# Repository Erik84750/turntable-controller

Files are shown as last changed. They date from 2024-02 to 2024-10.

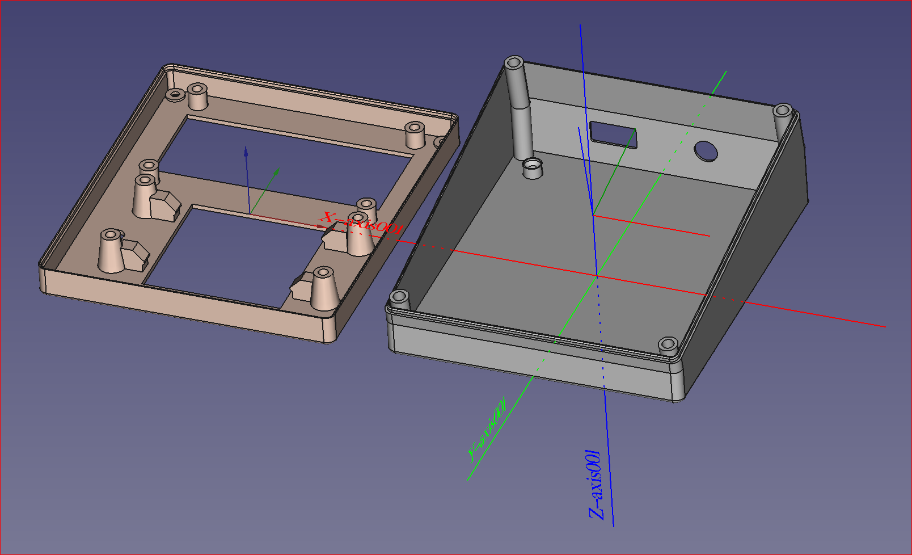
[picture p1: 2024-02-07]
turntable_controller_complete.png

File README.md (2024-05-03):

# turntable-controller
Digital stand-alone turntable controller with automated indexing and stepper motor

A. Introduction
  1. The purpose of this project is to create a stand-alone and automated model railroad (any scale) turntable controller
  2. Hardware: 

  a. stepper motor: project is usable for any type of stepper motor but prefered option is the use of a 17HS2408 motor (NEMA17).

  b. stepper motor driver: any motor driver module can be used but prefered option is a module with an onboard A4988 chip (https://lastminuteengineers.com/a4988-stepper-motor-driver-arduino-tutorial/).
    
  c. indexing sensor: optical HC-020K sensor with accurate positioning sensing; only the sensor (no perforated disks). Hall effect is exluded due to its inacurate sensing repeatability and wide detection range.
  The turntable disk should be equipped with just one small protruding object that passes through the sensor "eye", mounted underneath the framework, out of sight.
  The purpose being that this object passes through the sensor eye once every 360 degree rotation of the turntable.
This object may even be the size of a nail; as long as it passes through the sensor lips.
    
  d. 4x4 keypad with pushbuttons (no membrane keypad).
    
  e. a custom designed PCB (all required info for manufacture is included in this project file).
    
  f. LCD display with 20x4 characters.
    
  g. a 3D printable casing for this project, downloadable .stl files.

  h. turntable track polarity control: ACS712-based sensor controls the DCC track polarity. Omron G6S-2 5VDC relay. Measured reaction time is 2 microseonds (using AVR AtMega328 at 16MHs)! Therefor it beats every short-circuit or overload detection including the DCC-EX Command Station.
    
  3. Software
    a. C++ custom software with a very wide range of options and features
    b. All software is freely downloadable from this project file

B. Description of features:
  1. Any size of turntable can be controlled
  2. Automated initial indexing and storage in eeprom is provided. Due to the very high accuracy (+/- 1 micrometer) of the optical sensor the repeatability is < 5 micrometer.
  3. Fast index location and programming for outgoing/incoming tracks is provided, storage in eeprom. The turntable will always move CW or CCW after the algorithm included calculates the shortest/fastest rotation
  4. Automated "shortest rotation" algorithm is included in the software
  5. Photo-electric sensor (based on HC-020K module) http://tinyurl.com/2ce3v4j9 or http://tinyurl.com/3nykkvw3 used for indexing calibration
  6. button A: assign the current position to an index number in eeprom
  7. button B: move to whatever position by using the keypad
  8. button C: calibration
  9. button D: designate a position (current position) from eeprom to current turntable indexed position
  11. button #: select an index position to be moved to
  12. Button *: select index position + 180° to be moved to.
  13. enter # or * before index selection so that the turntable alligns at 0° or 180°
  14. Rotary encoder rotation of turntable; RE button serves to set speed x10 or regular
  15. a "long press" of (adjustable) 500ms is included to prevent inadvertent keypresses
  16. include, upon calibration, the option to make a full 360° in order to calculate the stepper motor steps for a full 360° rotation.
  17. EEPROM storage of programmed track index positions

C. Documents

[stepper motor 17HS2408-MotionKing.pdf](https://github.com/Erik84750/turntable-controller/files/14192960/stepper.motor.17HS2408-MotionKing.pdf)

[stepper motor driver A4988.pdf](https://github.com/Erik84750/turntable-controller/files/14192971/stepper.motor.driver.A4988.pdf)

[Uploading stepper motor 28BYJ-45 12V.pdf…]()

stepper motor HS2236_1

a4988-stepper-motor-controler

md-hc-020k

keypad 4x4

turntable_controller_complete



ACS712

Omron_G6S-2_5VDC

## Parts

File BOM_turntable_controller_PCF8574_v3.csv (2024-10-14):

Part | Value | Device | Package | Description | AVAILABILITY | DESCRIPTION | MF | MP | MPN | OC_FARNELL | OC_NEWARK | PACKAGE | PRICE | PURCHASE-URL
C1 | 47µF | CERAMIC-CAP | 1206 | ceramic capacitor leads 2.5mm and 5.5mm
C2 | 1µF | CERAMIC-CAP | 1206 | ceramic capacitor leads 2.5mm and 5.5mm
C3 | 100µF | CERAMIC-CAP | 1206 | ceramic capacitor leads 2.5mm and 5.5mm
C12 | 100µF | ELCOELCO3,5MMLEAD | ELCO-3.5MMLEAD | electrolytic capacitor 3.5mm lead
D1 | SCHOTTKY-SMA | SCHOTTKY-SMA | SMA-ALT | Schottky diode SMA package
D2 | pwr | LED-0603V1 | LED_0603 | LED SMD mount
D3 | SCHOTTKY-SMA | SCHOTTKY-SMA | SMA-ALT | Schottky diode SMA package
D4 |  | LED-0603V1 | LED_0603 | LED SMD mount
D5 |  | LED-0603V1 | LED_0603 | LED SMD mount
D6 |  | LED-0603V1 | LED_0603 | LED SMD mount
D7 |  | LED-0603V1 | LED_0603 | LED SMD mount
D8 | STEP | LED-0603V1 | LED_0603 | LED SMD mount
D9 | DIR | LED-0603V1 | LED_0603 | LED SMD mount
D10 | Enbl. | LED-0603V1 | LED_0603 | LED SMD mount
D11 | Vmot | LED-0603V1 | LED_0603 | LED SMD mount
IC1 | ARDUINO-PRO-MINI-LIMITED | ARDUINO-PRO-MINI-LIMITED | ARDUINO-PRO-MINI-LIMITED | Arduino Pro Mini Clone V1.0
IC2 | 7805 | LM78XX-TO220SINK_V2 | LM7805-SINK_V2 | LM1117 TO220 VOLTAGE REGULATOR
IC3 | PCF8574T | PCF8574T | SOIC127P1032X265-16N | Remote 8-bit I/O expander for I2C-bus Check availability | Not in stock | I/O Expander 8 I²C 100 kHz 20-SSOP | NXP Semiconductors | PCF8574T |  |  |  | SOIC-16 NXP Semiconductors | None
IC4 | ULN2003 | ULN2003 | SO16
JP1 | MS1 | JUMPER-SMT_2_NO_SILK | SMT-JUMPER_2_NO_SILK | Normally open jumper
JP2 | MS2 | JUMPER-SMT_2_NO_SILK | SMT-JUMPER_2_NO_SILK | Normally open jumper
JP3 |  | PINHD-1X2 | 1X02 | PIN HEADER
JP4 |  | PINHD-1X2 | 1X02 | PIN HEADER
JP5 |  | PINHD-1X8 | 1X08 | PIN HEADER
JP6 | MS3 | JUMPER-SMT_2_NO_SILK | SMT-JUMPER_2_NO_SILK | Normally open jumper
JP7 |  | PINHD-1X2 | 1X02 | PIN HEADER
JP9 |  | JUMPER-SMT_2_NO_SILK | SMT-JUMPER_2_NO_SILK | Normally open jumper
JP10 |  | JUMPER-SMT_2_NO_SILK | SMT-JUMPER_2_NO_SILK | Normally open jumper
JP11 |  | JUMPER-SMT_2_NO_SILK | SMT-JUMPER_2_NO_SILK | Normally open jumper
JP12 |  | JUMPER-SMT_2_NO_SILK | SMT-JUMPER_2_NO_SILK | Normally open jumper
R1 | 10k | RESISTORARRAY-0603 | RESISTORARRAY-0603 | Res Thick Film Array 100 Ohm 5% ?200ppm/C ISOL Epoxy 8-Pin 1206(4 X 0603) Convex SMD T/R Check availability | In Stock | 330 Ohm ±5% 62.5mW Power Per Element Isolated 4 Resistor Network/Array ±200ppm/°C 1206 (3216 Metric), Convex, Long Side Terminals | Yageo | YC164-JR-07330RL |  |  |  | 1206 Yageo | None | https://pricing.snapeda.com/search/part/YC164-JR-07330RL/?ref=eda
R2 | 4k7 | RESISTORARRAY-0603 | RESISTORARRAY-0603 | Res Thick Film Array 100 Ohm 5% ?200ppm/C ISOL Epoxy 8-Pin 1206(4 X 0603) Convex SMD T/R Check availability | In Stock | 330 Ohm ±5% 62.5mW Power Per Element Isolated 4 Resistor Network/Array ±200ppm/°C 1206 (3216 Metric), Convex, Long Side Terminals | Yageo | YC164-JR-07330RL |  |  |  | 1206 Yageo | None | https://pricing.snapeda.com/search/part/YC164-JR-07330RL/?ref=eda
R3 | 10k | RESISTOR-SMD-1206 | R1206W | Resistor 1/4W H wide fit
R5 | 10k | RESISTOR-SMD-1206 | R1206W | Resistor 1/4W H wide fit
R6 | 4k7 | RESISTORARRAY-0603 | RESISTORARRAY-0603 | Res Thick Film Array 100 Ohm 5% ?200ppm/C ISOL Epoxy 8-Pin 1206(4 X 0603) Convex SMD T/R Check availability | In Stock | 330 Ohm ±5% 62.5mW Power Per Element Isolated 4 Resistor Network/Array ±200ppm/°C 1206 (3216 Metric), Convex, Long Side Terminals | Yageo | YC164-JR-07330RL |  |  |  | 1206 Yageo | None | https://pricing.snapeda.com/search/part/YC164-JR-07330RL/?ref=eda
U$9 | JST-XH-5 | JST-XH-5 | B5B-XH-A
U1 | A4988 | A4988 | A4988 | Stepper motor controler; IC: A4988; 1A; Uin mot: 8÷35V Check availability | Not in stock | Stepper Motor Driver | Pololu | A4988 STEPPER MOTOR DRIVER CARRIER |  |  |  | None | None
X1 |  | TERMINAL-5MM-2POLE | W237-132 | WAGO SREW CLAMP |  |  |  |  |  | unknown | unknown
X2 | TERMINAL_2P_3,5MM_V2 | TERMINAL_2P_3,5MM_V2 | TERMINAL_2P_3,5MM_V2 | MKDS 1/ 2-3,5 Printklemme |  |  |  |  |  | unknown | unknown
X3 | TERMINAL_2P_3,5MM_V2 | TERMINAL_2P_3,5MM_V2 | TERMINAL_2P_3,5MM_V2 | MKDS 1/ 2-3,5 Printklemme |  |  |  |  |  | unknown | unknown
X4 | TERMINAL_2P_3,5MM_V2 | TERMINAL_2P_3,5MM_V2 | TERMINAL_2P_3,5MM_V2 | MKDS 1/ 2-3,5 Printklemme |  |  |  |  |  | unknown | unknown
X5 | TERMINAL_2P_3,5MM_V2 | TERMINAL_2P_3,5MM_V2 | TERMINAL_2P_3,5MM_V2 | MKDS 1/ 2-3,5 Printklemme |  |  |  |  |  | unknown | unknown
X6 | TERMINAL_2P_3,5MM_V2 | TERMINAL_2P_3,5MM_V2 | TERMINAL_2P_3,5MM_V2 | MKDS 1/ 2-3,5 Printklemme |  |  |  |  |  | unknown | unknown
X7 | TERMINAL_2P_3,5MM_V2 | TERMINAL_2P_3,5MM_V2 | TERMINAL_2P_3,5MM_V2 | MKDS 1/ 2-3,5 Printklemme |  |  |  |  |  | unknown | unknown
X8 |  | TERMINAL-5MM-2POLE | W237-132 | WAGO SREW CLAMP |  |  |  |  |  | unknown | unknown
X9 | TERMINAL_2P_3,5MM_V2 | TERMINAL_2P_3,5MM_V2 | TERMINAL_2P_3,5MM_V2 | MKDS 1/ 2-3,5 Printklemme |  |  |  |  |  | unknown | unknown
X10 | TERMINAL_2P_3,5MM_V2 | TERMINAL_2P_3,5MM_V2 | TERMINAL_2P_3,5MM_V2 | MKDS 1/ 2-3,5 Printklemme |  |  |  |  |  | unknown | unknown
X11 | TERMINAL_2P_3,5MM_V2 | TERMINAL_2P_3,5MM_V2 | TERMINAL_2P_3,5MM_V2 | MKDS 1/ 2-3,5 Printklemme |  |  |  |  |  | unknown | unknown
X12 | TERMINAL_2P_3,5MM_V2 | TERMINAL_2P_3,5MM_V2 | TERMINAL_2P_3,5MM_V2 | MKDS 1/ 2-3,5 Printklemme |  |  |  |  |  | unknown | unknown
X13 | TERMINAL_2P_3,5MM_V2 | TERMINAL_2P_3,5MM_V2 | TERMINAL_2P_3,5MM_V2 | MKDS 1/ 2-3,5 Printklemme |  |  |  |  |  | unknown | unknown
X14 | JST-XH-04 | JST-XH-04 | B4B-XH-A | JST XH Connector 2 Pin

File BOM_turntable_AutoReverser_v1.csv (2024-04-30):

Part | Value | Device | Package | Description | MF | MPN | OC_FARNELL | OC_NEWARK
C1 | 100µF | CERAMIC-CAP | 1206 | ceramic capacitor leads 2.5mm and 5.5mm
D2 | LED-0603 | LED-0603V1 | LED_0603 | LED SMD mount
D3 | 1N4148 | 1N4148SOD323-ST | SOD323_ST | DIODE
IC1 | ARDUINO-PRO-MINI-LIMITED | ARDUINO-PRO-MINI-LIMITED | ARDUINO-PRO-MINI-LIMITED | Arduino Pro Mini Clone V1.0
IC2 | LM7111-5V | LM1117-TO220 | TO220V | LM1117 TO220 VOLTAGE REGULATOR
JP1 |  | PINHD-1X3 | 1X03 | PIN HEADER
K1 | OMRON_RELAY_TX25VD2 | OMRON_RELAY_TX25VD2 | RELAY | TX Relais NAiS |  | TXD2-5V | unknown
Q1 | AO3400A | AO3400A-N-CH | SOT23 | AO3400 N-channel 30V TTL MOSFET
R1 | 1k | RESISTOR-SMD-1206 | R1206W | Resistor 1/4W H wide fit
R2 | 1k | RESISTOR-SMD-1206 | R1206W | Resistor 1/4W H wide fit
SJ1 |  | SJ | SJ | SMD solder JUMPER
X1 | TERMINAL_2P_3,5MM_V2 | TERMINAL_2P_3,5MM_V2 | TERMINAL_2P_3,5MM_V2 | MKDS 1/ 2-3,5 Printklemme |  |  | unknown | unknown
X2 | TERMINAL_2P_3,5MM_V2 | TERMINAL_2P_3,5MM_V2 | TERMINAL_2P_3,5MM_V2 | MKDS 1/ 2-3,5 Printklemme |  |  | unknown | unknown
X5 |  | TERMINAL-5MM-2POLE | W237-132 | WAGO SCREW CLAMP |  |  | unknown | unknown
X6 |  | TERMINAL-5MM-2POLE | W237-132 | WAGO SCREW CLAMP |  |  | unknown | unknown

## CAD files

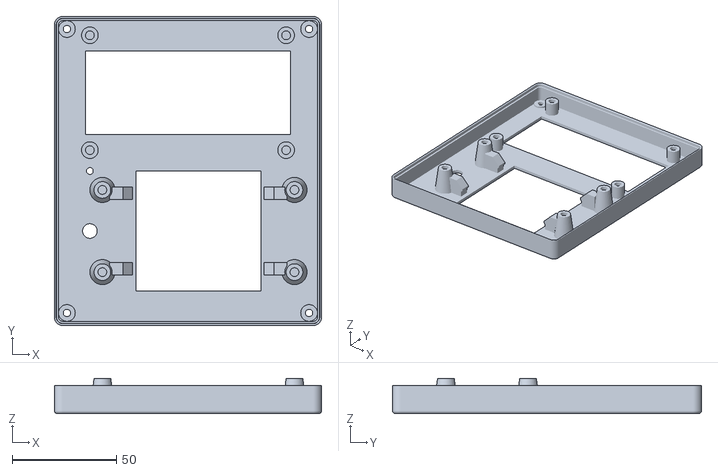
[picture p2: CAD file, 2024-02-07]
turntable_controller_v2-cover.stl
128.0 x 148.0 x 17.0

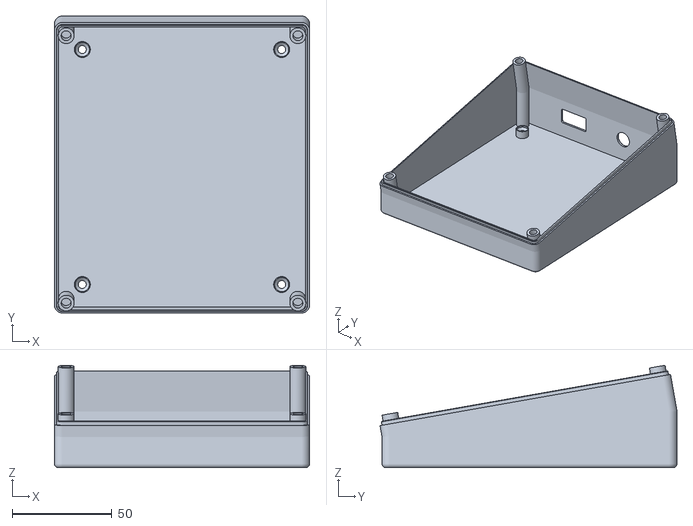
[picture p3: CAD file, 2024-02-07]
turntable_controller_v2-bottom.stl
128.0 x 149.0 x 51.4

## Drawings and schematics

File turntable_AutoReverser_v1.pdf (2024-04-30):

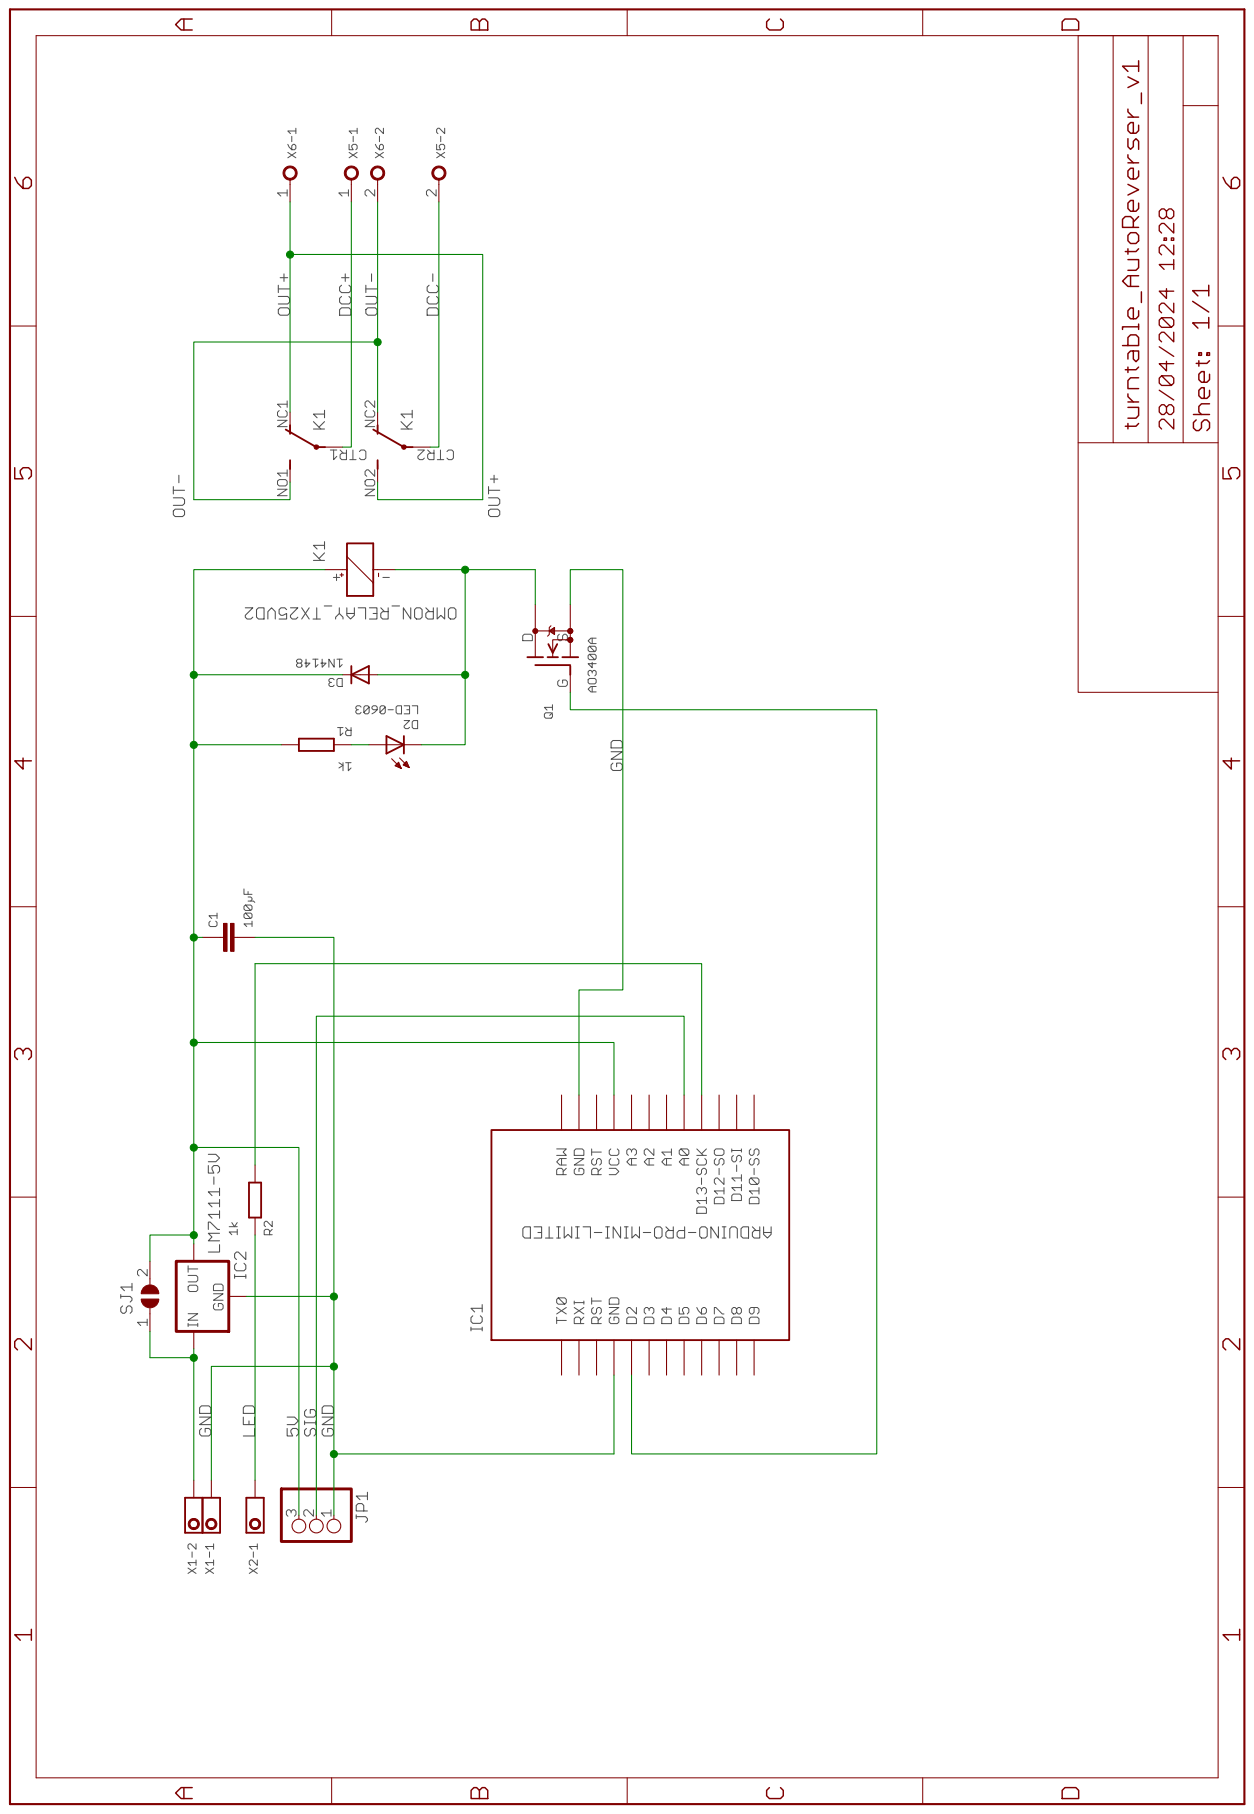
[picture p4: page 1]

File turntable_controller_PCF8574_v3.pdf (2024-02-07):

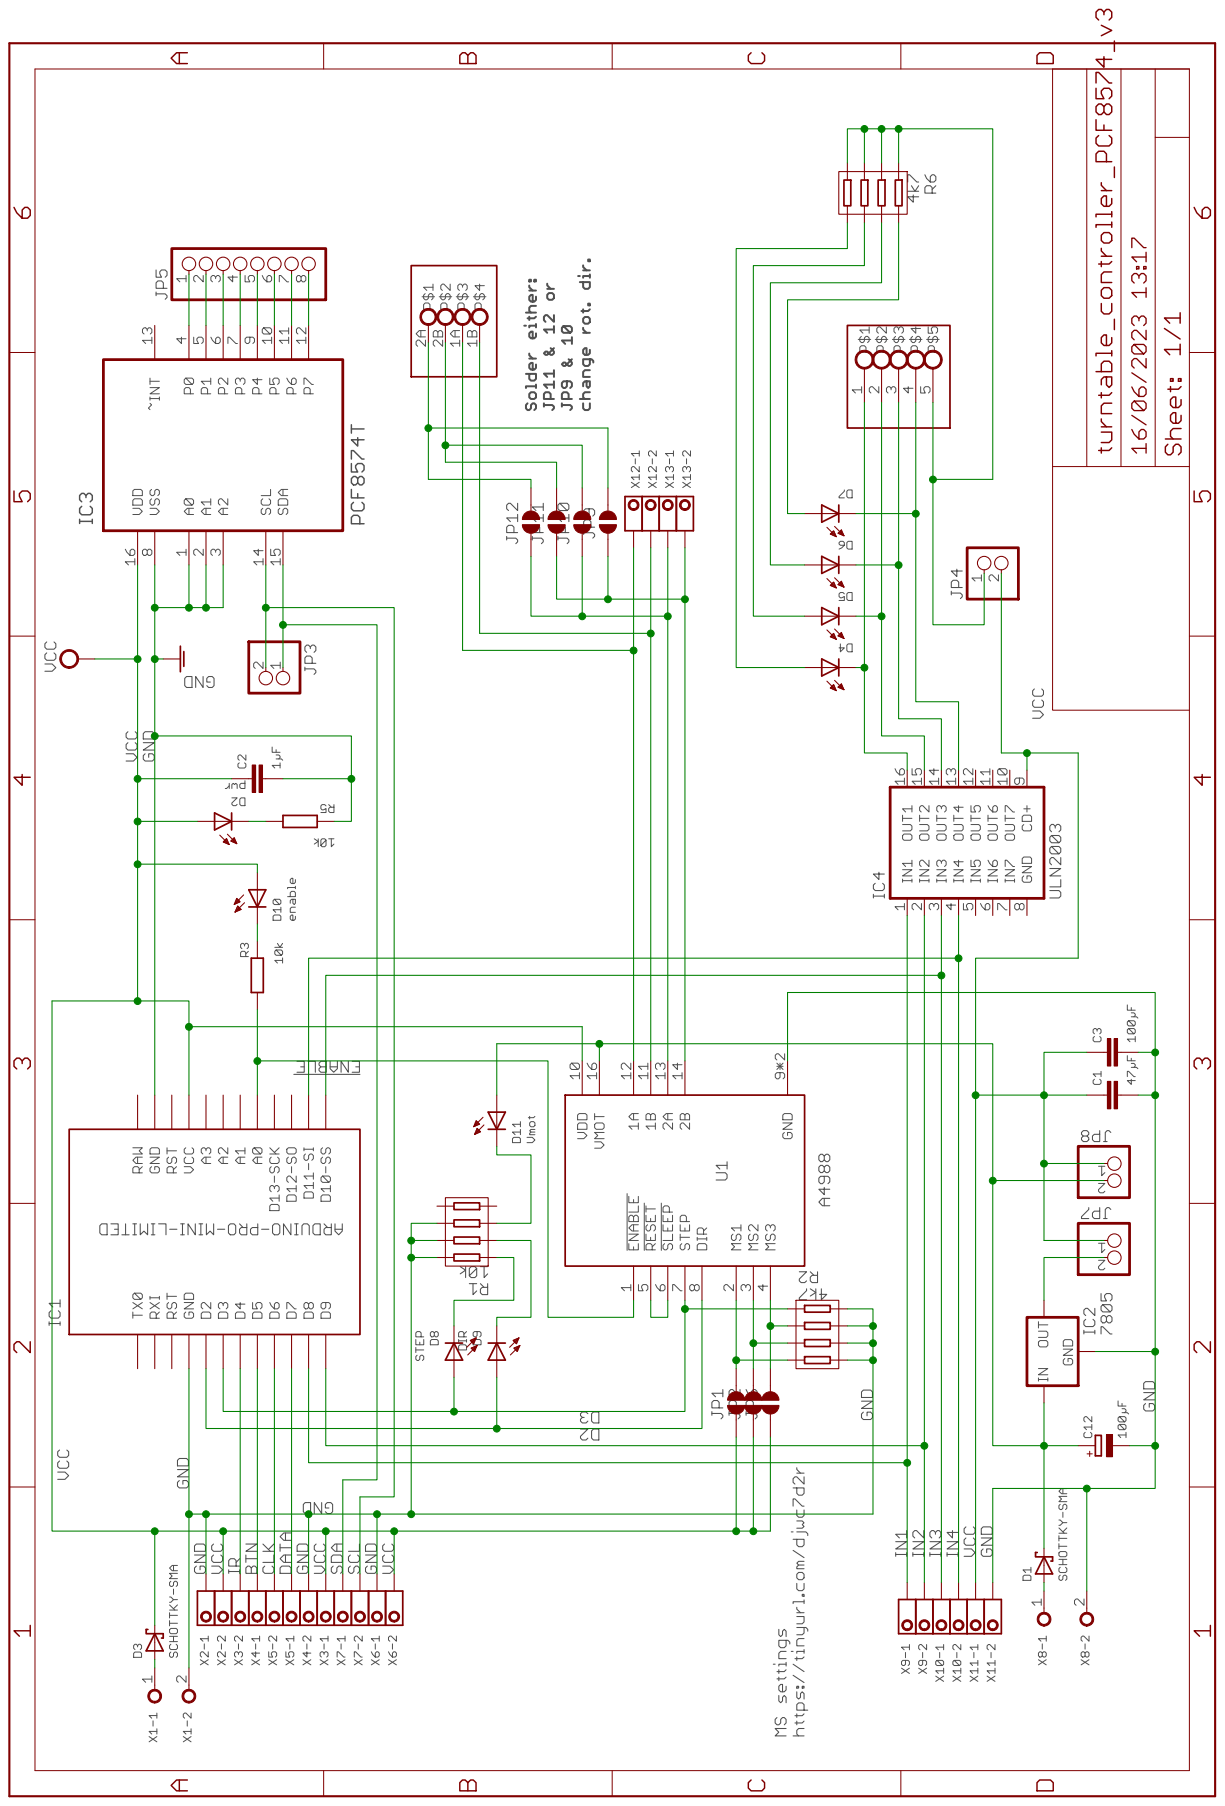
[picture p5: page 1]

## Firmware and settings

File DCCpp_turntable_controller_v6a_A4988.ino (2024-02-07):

/*
  Read keypad: if number pressed then two keypad strokes required; else just one stroke
  Store keypad numerical entry for
     OBSOLETE 1. either turntable index position (moveTo
     OBSOLETE 2. or store in EEPROM after 'A' is pressed
  Store character entry for:
     A = Assign current position (currentPosition) into eeprom for an index number (index to be entered)
     B = move to whatever position value is entered in keypad
          # = validate numerical entry (for >2 digits only; ie: case B
            = erase last numerical entry, for case B only
     C = calibration of '0' index position; optionally turn table 360 degrees to calculate number of steps needed for 180 degrees
     D = Designate a position (setCurrentPosition) from eeprom to current turntable indexed position (index to be entered):
         done at program startup when stepper is in a known and indexed position
     # = select index position to be moved to
     * = select index position + 180 degrees to be moved to

       NOTE: v5 : precede index with either # or * to decide allignement of turntable at 0 or 180 degrees

  Version v5:
  1. also allow indexposition + 180 degrees: allow the turntable to make a half turn on the same index
  2. index selection: now precede with either # or  * to decide whether turntable alligns at 0 degrees ort 180 degrees

  Version v6:
     1. done: to do: on calibration give option to make a full 360 degree turn, to count the number of required steps.
     This in order to calculate the number of steps needed to make a 18 degree swing
     2. to do: index selection: now precede with either # or  * to decide whether turntable alligns at 0 degrees or 180 degrees
     3. done: to do: optimize index search (see 2.) for minimum distance movement (algorithm)
     4. done: introduce a "long press" for keypad characters: https://arduinogetstarted.com/tutorials/arduino-button-long-press-short-press
     5. introduce a turntable movement interruption, for example when wrong index is selected; to avoid having to wait for turntable to finalise the wrong move

  Version 6a:
     1. modified algorithm "shortest move" to accomodate for the special case (re Thomas 9/6/23)

  Turntable notes: 120' scale Diamond Scale Model
  Circumference : 141.3cm
  Stepper: 28BYJ-48. gear ratio = 1/63,68395 approx 1/64.
  32 steps/revolution with gear : 32 x 64 = 2038 steps/revolution
  With 1/50 worm gear: 2038 x 50 = 101.900 steps / revolution
  with circumference of 1413mm gives 0,01387mm / step
  With 1ms/step and 101.900 steps/revolution and 60.000 ms/minute = 0,588 rpm
  Without 1/50 wormgear: 29rpm
  Measured max stepper speed: 2:26' for 50 revolutions, = 1 revolution per 2.92 second, = 20 rpm
  Actual speed measurement: 10 revolutions 32" (with accel and decel)
  With 50/1 gear ratio: 0.411 rpm

  NOTE: from accelstepper.h documentation, fastest speed is 4000 steps/second at 16MHz
  https://forum.arduino.cc/t/maximum-speed-using-accelstepper/1059990/6

  video on a Diamond Scale stepper-driven turntable: https://www.youtube.com/watch?v=9iM3EE5VJwk
  How to input multiple digit numbers on keypad https://forum.arduino.cc/t/keypad-input-2-digit-numbers/604861
  How to deal wth both 2-digit numbers as with character keypad input https://forum.arduino.cc/t/keypad-numericals-ok-now-letters-how-to/1128871/8
  How to accumulate and store two numerical entries: https://forum.arduino.cc/t/keypad-how-to-accumulate-and-store-two-numerical-entries/1127280
  How to enter letters besides numericals: https://forum.arduino.cc/t/keypad-numericals-ok-now-letters-how-to/1128871/8
  In-depth analysis of stepper 28BYJ-48 https://lastminuteengineers.com/28byj48-stepper-motor-arduino-tutorial/
  How to simulate a program workflow: https://forum.arduino.cc/t/blocking-while/1129972/8
  How to reduce dynamic memory consumption: https://forum.arduino.cc/t/uno-global-variables-consume-84/1130251/4
  How to reduce dynamic memory size: https://forum.arduino.cc/t/uno-global-variables-consume-84/1130251/8
  How to long press: https://arduinogetstarted.com/tutorials/arduino-button-long-press-short-press
  PROGMEM reference: http://www.gammon.com.au/progmem
  EEPROM: https://roboticsbackend.com/arduino-store-int-into-eeprom/
          https://docs.arduino.cc/learn/built-in-libraries/eeprom
          https://stackoverflow.com/questions/67201612/differences-for-eeprom-read-and-eeprom-get
          https://www.best-microcontroller-projects.com/arduino-eeprom.html#:%7E:text=Arduino%20EEPROM%20get%20vs%20read,bytes%20starting%20from%20an%20address
  A4988 stepper driver: https://lastminuteengineers.com/a4988-stepper-motor-driver-arduino-tutorial/
                        https://all3dp.com/2/vref-calculator-tmc2209-tmc2208-a4988/
  A4988 microstep resolution
  MS1 MS2 MS3
  L   L   L   full step (default)
  H   L   L   1/2 step
  L   H   L   1/4 step
  H   H   L   1/8 step
  H   H   H   1/16 step

  NEMA17 stepper connections: https://mecha4makers.co.nz/product/17hs2408-stepper-motor-5mm-shaft-without-flat/
  6 Pin JST PH6 (6 pin, 2mm pitch) male socket:
    Pin 1: A+ / 1A
    Pin 2: NC
    Pin 3: B+ / 2A
    Pin 4: A- / 1B
    Pin 5: NC
    Pin 6: B- / 2B





*/
#include "Wire.h"
#include "I2CKeyPad.h"  // https://github.com/RobTillaart/I2CKeyPad
#include <EEPROM.h>
#include <LCD.h> // https://forum.arduino.cc/t/lcd-i2c-libraries-incompatibility/968205
#include <LiquidCrystal_I2C.h>  // https://github.com/fmalpartida/New-LiquidCrystal/blob/master/LiquidCrystal_I2C.h
#include <AccelStepper.h>
#include <avr/pgmspace.h>

#define motorInterfaceType 1
/*
  FUNCTION  = 0, ///< Use the functional interface, implementing your own driver functions (internal use only)
  DRIVER    = 1, ///< Stepper Driver, 2 driver pins required
  FULL2WIRE = 2, ///< 2 wire stepper, 2 motor pins required
  FULL3WIRE = 3, ///< 3 wire stepper, such as HDD spindle, 3 motor pins required
  FULL4WIRE = 4, ///< 4 wire full stepper, 4 motor pins required
  HALF3WIRE = 6, ///< 3 wire half stepper, such as HDD spindle, 3 motor pins required
  HALF4WIRE = 8  ///< 4 wire half stepper, 4 motor pins required
*/
#define MP1  8 // IN1 on the ULN2003
#define MP2  9 // IN2 on the ULN2003
#define MP3  10 // IN3 on the ULN2003
#define MP4  11 // IN4 on the ULN2003
#define ledIR 4 // input for IR led detector, HIGH when NO detection
#define LCD_ADDR     0x27 // LCD I2C address
#define clk 6   //Clock pin connected to D6
#define data 7    //Data pin connected to D7
#define ENC_SWITCH 5   //Push button pin connected to D5
#define led 13  // built-in led
#define enable A0

const uint8_t KEYPAD_ADDRESS = 0x38; // PCF8574 = 0x20  PCF8574AP = 0x38
const int dirPin = 2;
const int stepPin = 3;

char keys[] = "123A456B789C*0#DNF";  // N = NoKey, F = Fail (e.g. >1 keys pressed)
uint8_t i; // identifier for either number (i = 1 ... = number of numbers), or character : i = (0, or) 50
uint8_t ttMaxPos = 15; // maximum number of indexed turntable positions
// Set Encoder values
volatile int32_t stepperPosition = 0;
int32_t prevPosition;
const uint16_t disableDelay = 1000;
const uint16_t keyLongPress = 500;  // minimum time in ms for keypad long press
bool newData, runOk, tempBtn, btnState, ledState, currentBtnState; // booleans for new data from serial, and run allowed flag
bool stepperInUse = false;
bool driverEnabled = false;
bool caseIdx = false;
bool caseReady = false;
bool valueReady = false;
bool indexReady = false;

// char keyVal = 0;   // the actual key pressed
uint8_t index = 0;  // index for keypad array

uint8_t speed = 1;
uint32_t totalSteps180, pressedTime, releasedTime, pressDuration;  // number of steps for half a turntable turnstored in eeprom address 500
bool currentState;  // keypad long-press variables

// Create myStepper instance
// Pins entered in sequence IN1-IN3-IN2-IN4 for proper step sequence
// AccelStepper myStepper(MotorInterfaceType, 8, 10, 9, 11);
//  AccelStepper myStepper(MotorInterfaceType, MP1, MP3, MP2, MP4);  //Define the pin sequence (IN1-IN3-IN2-IN4). Coil sequence: 1A-1B-2B-2A
AccelStepper myStepper(motorInterfaceType, stepPin, dirPin);
I2CKeyPad keyPad(KEYPAD_ADDRESS);
LiquidCrystal_I2C lcd(LCD_ADDR, 2, 1, 0, 4, 5, 6, 7, 3, POSITIVE);

///|||||||||||||||||||||||||||||||||||||||||||||||||||///
///                   setup                           ///
///|||||||||||||||||||||||||||||||||||||||||||||||||||///

void setup() {
  Wire.begin();
  Serial.begin(9600);
  Serial.println(F("DCCpp_turntable_controller_v6a_A4988"));


  // Encoder interupt pins
  pinMode(ENC_SWITCH, INPUT_PULLUP);
  pinMode(clk, INPUT_PULLUP);
  pinMode(data, INPUT_PULLUP);
  pinMode(led, OUTPUT);
  digitalWrite(led, LOW);
  pinMode(enable, OUTPUT);
  digitalWrite(enable, HIGH);

  // Activate pin change interruptions on pin D6 and D7
  PCICR |= (1 << PCIE2);      // set PCICR register bit 2 (PCIE2: PCINT[23:16], 0B00000100) this is for PD0 to PD7
  PCMSK2 |= (1 << PCINT22);   // pin 6 PCINT22, 0B01000000    interrupt from pin 6
  PCMSK2 |= (1 << PCINT23);   // pin 7 PCINT23, 0B10000000    interrupt from pin 7

  // set the maximum speed, acceleration factor,
  // initial speed and the target position
  myStepper.setMaxSpeed(700.0);
  myStepper.setAcceleration(100.0);
  //myStepper.setSpeed(200);
  myStepper.moveTo(0);

  lcd.begin(20, 4);               // initialize the LCD
  lcd.setCursor(1, 0); // starts  column 0..19, row 0..3
  lcd.print(F("DCCpp_tt_ctrlr_v6a"));

  if (keyPad.begin() == false)
  {
    Serial.println(F("\nERROR: cannot communicate to keypad.\nPlease reboot.\n"));
    lcd.setCursor(1, 0); // starts  column 0..19, row 0..3
    lcd.print(F("keypad comms error"));
    while (1);
  }

}

///|||||||||||||||||||||||||||||||||||||||||||||||||||///  // each pulse from the RE causes one interrupt
///               IRQ routine                         ///
///|||||||||||||||||||||||||||||||||||||||||||||||||||///

ISR(PCINT2_vect) {
  static uint8_t lastStateClock;
  uint8_t currentStateClock = (PIND & 0B01000000);  //  Pin D6 state
  uint8_t stateData = (PIND & 0B10000000);  //  Pin D7 state
  stateData = stateData >> 1;   // shift right one bit: for PD7 move 0Bx0000000 to 0B0x000000 to be on the same level as PD6
  if ( currentStateClock != lastStateClock )
  {
    // If D7 state is different from D6 state, then encoder is rotating clockwise
    if (stateData != currentStateClock)
      stepperPosition += speed;                        //  increment
    //Else, the encoder is rotating counter-clockwise
    else
      stepperPosition -= speed;                        //  decrement
    lastStateClock = currentStateClock;         // Updates the previous state of the clock with the current state
  }
}

///|||||||||||||||||||||||||||||||||||||||||||||||||||///
///                   loop                            ///
///|||||||||||||||||||||||||||||||||||||||||||||||||||///

void loop() {
  static bool keyPress = true;
  static int myValue = 0;
  static bool pressed = false;
  static char str = 0;

  myStepper.run();  // activate stepper if distanceToGo is not yet 0


  // Check for encoder update from interrupt routine; requires one pulse (one interrupt) for this to be executed
  if (stepperPosition != prevPosition) {
    digitalWrite(enable, LOW);  // enable stepper output    // driverEnabled = true;
    myStepper.moveTo(stepperPosition);
    stepperInUse = true;
    myStepper.enableOutputs();
    driverEnabled = true;
    prevPosition = stepperPosition;
  }

  // check if rotary encoder button is pressed: RE speed selection
  if (readEncSwitch()) {
    if ( !pressed ) {
      speed = (speed == 1 ? 10 : 1);
      digitalWrite(led, (speed == 10 ? HIGH : LOW));
      pressed = true;
      Serial.println(speed);
    }
  }
  else pressed = false;

  disableStepper();

  // press a character key:
  // since v5: preceed with # or * to decide on straight or 180 degrees reversed turntable positioning DONE
  // !! Also calculate if CW or CCW is shortest distance !! DONE

  if (!keyPad.isPressed()) keyPress = true; // set flag keyPress: keypad released. Long press is detected after release.
  if (keyPad.isPressed () && keyPress == true) {  // execute only once
    keyPress = false;
    pressedTime = millis();  // button is pressed
    currentState = true;
    Serial.println(F("pressedTime is set"));
    myValue = getKeypadInput(myValue); // read keypad being pressed, is always a number; if character then the ASCII number for that character
    lcd.clear();
    lcd.setCursor(0, 0);  // starts  column 0..19, row 0..3
    lcd.print(F("apply long key press"));
  }
  if (currentState) { // button has been pressed and may still be pressed
    if (!keyPad.isPressed()) { // keypad is released
      releasedTime = millis();  // release time
      pressDuration = releasedTime - pressedTime;

      if (pressDuration > keyLongPress) { // button was pressed long enough
        Serial.print(F("pressduration = "));
        Serial.println(pressDuration);
        Serial.println(F("keypad is pressed long enough"));
        // myValue = getKeypadPress(myValue); // read keypad being pressed, is always a number; if character then the ASCII number for that character

        Serial.print(F("charater pressed = "));
        Serial.println(myValue);
        Serial.print(F("i = "));
        Serial.println(i);
        Serial.print(F("i in currenState = "));
        Serial.println(i);
        if (i < 50) { // a numerical was pressed
          Serial.println("wrong key, press character key");
          lcd.setCursor(0, 1);  // starts  column 0..19, row 0..3
          lcd.print(F("wrong key, use char"));
        }
        else {  // a character or # or * was pressed
          str = myValue; // convert number to character
          myValue = 0;
          lcd.clear();
          lcd.setCursor(0, 0);  // starts  column 0..19, row 0..3
          lcd.print(F("key request:      "));
          lcd.setCursor(16, 0);  // starts  column 0..19, row 0..3
          lcd.print(str);  // print character on line 0
          Serial.print(F("letter obtained : "));
          Serial.println(str);
          keypadAction(str);  // go to switch case
          // str = 0;
        }
        i = 0;
      }
      else {
        Serial.println(F("button press not long enough"));
        lcd.print(F("key not pressed long"));
      }
      currentState = false;
    }
  }
}

///|||||||||||||||||||||||||||||||||||||||||||||||||||///
///               disable stepper output             ///
///|||||||||||||||||||||||||||||||||||||||||||||||||||///

void disableStepper() {
  static uint32_t timeStepped = 0;

  // Disable outputs once stepperPosition reached
  if (stepperInUse) {  // initialize ouput disable
    if ( myStepper.distanceToGo() == 0 ) {
      stepperInUse = false;
      timeStepped = millis();
      Serial.println(F("stepperInUse = true"));
    }
  }
  else if (driverEnabled && (millis() - timeStepped) >= disableDelay) {     // start disable after timeout disableDelay
    digitalWrite(enable, HIGH);
    myStepper.disableOutputs();
    driverEnabled = false;
    caseReady = true;
    valueReady = false;
    stepperPosition = myStepper.currentPosition(); // set global variable equal to current stepper position
    prevPosition = stepperPosition;
    Serial.print(F("Position: "));
    Serial.println(stepperPosition);
    lcd.clear();
    lcd.setCursor(0, 0);  // starts  column 0..19, row 0..3
    lcd.print(F("stepper disabled"));
    lcd.setCursor(0, 1);  // starts  column 0..19, row 0..3
    lcd.print(F("Position: "));
    lcd.setCursor(10, 1);  // starts  column 0..19, row 0..3
    lcd.print(stepperPosition);
  }
}


///|||||||||||||||||||||||||||||||||||||||||||||||||||///
///          get integer or char from keypad          ///
///|||||||||||||||||||||||||||||||||||||||||||||||||||///

int getKeypadInput(int value) {
  bool isNum = 0;
  char keyVal = 0;   // the actual key pressed

  do  {
    index = keyPad.getKey();                          // input the key
    keyVal = keys[index];
    isNum = (keyVal >= '0' && keyVal <= '9');         // is it a digit?
    char str = keyVal;
    Serial.print(F("index in getKeypadPress = "));
    Serial.println(index);
    Serial.print(F("str in getKeypadPress = "));
    Serial.println(str);

    if (isNum) {
      // i = i + 1;
      i += 1;
      //Serial.print(keyVal - '0');
      value = value * 10 + keyVal - '0';               // accumulate the input number
    }
    if (keyVal == 'A' || keyVal == 'B' || keyVal == 'C' || keyVal == 'D' || keyVal == '*' || keyVal == '#') {
      i = 50;  // sets the flag for non-numerical value entered
      Serial.print(F("i in getKeypadPress = "));
      Serial.println(i);
      value = keyVal;
    }
  }
  while ( !keyVal);       // exit do when a kay was pressed
  return value;
}


///|||||||||||||||||||||||||||||||||||||||||||||||||||///
///          read rotary encoder button               ///
///|||||||||||||||||||||||||||||||||||||||||||||||||||///

int readEncSwitch() {
  // Switch debounce values
  uint16_t debounce = 30;    // maybe 50 is enough
  static uint32_t lTimeOfChange = 0;  // Time when button state changed
  static int16_t lastStatus = 0;

  if ((millis() - lTimeOfChange) >= debounce) {
    int encSwitch = !digitalRead(ENC_SWITCH);  // Read the Encoder switch (low when pressed so invert)

    if (encSwitch != lastStatus) {
      lastStatus = encSwitch;
      lTimeOfChange = millis();
    }
  }
  return lastStatus;
}


///|||||||||||||||||||||||||||||||||||||||||||||||||||///  https://roboticsbackend.com/arduino-store-int-into-eeprom/
///   writing integers to eeprom, max. 65.535       ///
///|||||||||||||||||||||||||||||||||||||||||||||||||||///

void intToEEPROM(uint16_t address, int16_t number) {
  EEPROM.update(address, number >> 8);
  EEPROM.update(address + 1, number & 0xFF);
}

///|||||||||||||||||||||||||||||||||||||||||||||||||||///  https://roboticsbackend.com/arduino-store-int-into-eeprom/
///   reading integers from eeprom, max. 65.535       ///
///|||||||||||||||||||||||||||||||||||||||||||||||||||///

uint16_t intFromEEPROM(uint16_t address) {
  return (EEPROM.read(address) << 8) + EEPROM.read(address + 1);
}

///|||||||||||||||||||||||||||||||||||||||||||||||||||///  https://roboticsbackend.com/arduino-store-int-into-eeprom/
///      writing long to eeprom, max. 4x10sq9         ///
///|||||||||||||||||||||||||||||||||||||||||||||||||||///

void writeLongIntoEEPROM(uint16_t address, int32_t number) {
  EEPROM.update(address, (number >> 24) & 0xFF);
  EEPROM.update(address + 1, (number >> 16) & 0xFF);
  EEPROM.update(address + 2, (number >> 8) & 0xFF);
  EEPROM.update(address + 3, number & 0xFF);
}

///|||||||||||||||||||||||||||||||||||||||||||||||||||///  https://roboticsbackend.com/arduino-store-int-into-eeprom/
///      reading long from eeprom, max. 4x10sq9       ///
///|||||||||||||||||||||||||||||||||||||||||||||||||||///

int32_t readLongFromEEPROM(uint16_t address) {
  return ((long)EEPROM.read(address) << 24) +
         ((long)EEPROM.read(address + 1) << 16) +
         ((long)EEPROM.read(address + 2) << 8) +
         (long)EEPROM.read(address + 3);
}

///|||||||||||||||||||||||||||||||||||||||||||||||||||///
///          keypad character entries                 ///
///|||||||||||||||||||||||||||||||||||||||||||||||||||///
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

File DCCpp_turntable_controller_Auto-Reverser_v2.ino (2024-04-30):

//Autoreverser 1.0 (2020-12-25)
// DCC Isolated Autoreversing circuit for turntable track
// A0 pin connected to the out pin of the ACS712 current sensor
// D2 pin connected to the gate of the MOSFET, driving the relay
/*

  https://www.trainboard.com/highball/index.php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

*/

//
//    FILE: ACS712_20_DC.ino
// Adapted from AUTHOR: Rob Tillaart
// PURPOSE: demo for AutoReversing circuit for DCC turntable track polarity reversal
//     URL: https://github.com/RobTillaart/ACS712
//
//  use with Arduino Serial Plotter/Monitor


#include "ACS712.h"
#define relay 2
#define led 13
bool relayState = false;

//  Arduino UNO has 5.0 volt with a max ADC value of 1023 steps
//  ACS712 5A  uses 185 mV per A
//  ACS712 20A uses 100 mV per A
//  ACS712 30A uses  66 mV per A

ACS712  ACS(A0, 5.0, 1023, 185);
//  ESP 32 example (might requires resistors to step down the logic voltage)
//  ACS712  ACS(25, 3.3, 4095, 185);

void setup()
{
  Serial.begin(115200);
  while (!Serial);
  Serial.println(__FILE__);
  Serial.print("ACS712_LIB_VERSION: ");
  Serial.println(ACS712_LIB_VERSION);

  ACS.autoMidPoint();
  //  Serial.println(ACS.getMidPoint());
  pinMode(relay, OUTPUT);
  pinMode(led, OUTPUT);
}

void loop()
{
  int mA = abs(ACS.mA_DC());
  Serial.println(mA);    // comment out to increase loop speed

  if (mA > 1500 && relayState == false)
  {
    digitalWrite(relay, HIGH);
    digitalWrite(led, HIGH);
    relayState = true;
    delay(500);
  }
  else if (mA > 1500 && relayState == true)
  {
    digitalWrite(relay, LOW);
    digitalWrite(led, LOW);
    relayState = false;
    delay(500);
  }
  // delay(50);  // reduce delay to less than the time required by the DCC++/EX power booster to shut down due to a true short circuit.
}


//  -- END OF FILE --
